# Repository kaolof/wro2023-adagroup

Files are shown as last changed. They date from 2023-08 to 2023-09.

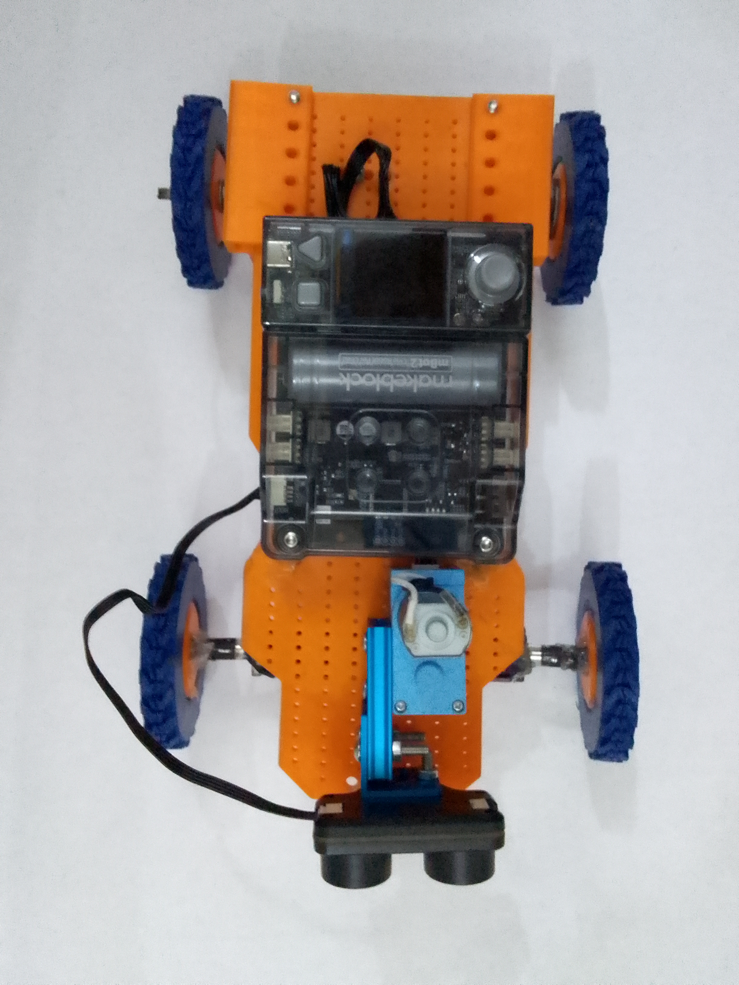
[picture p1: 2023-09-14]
v-photos/IMG_20230913_215858_856.jpg

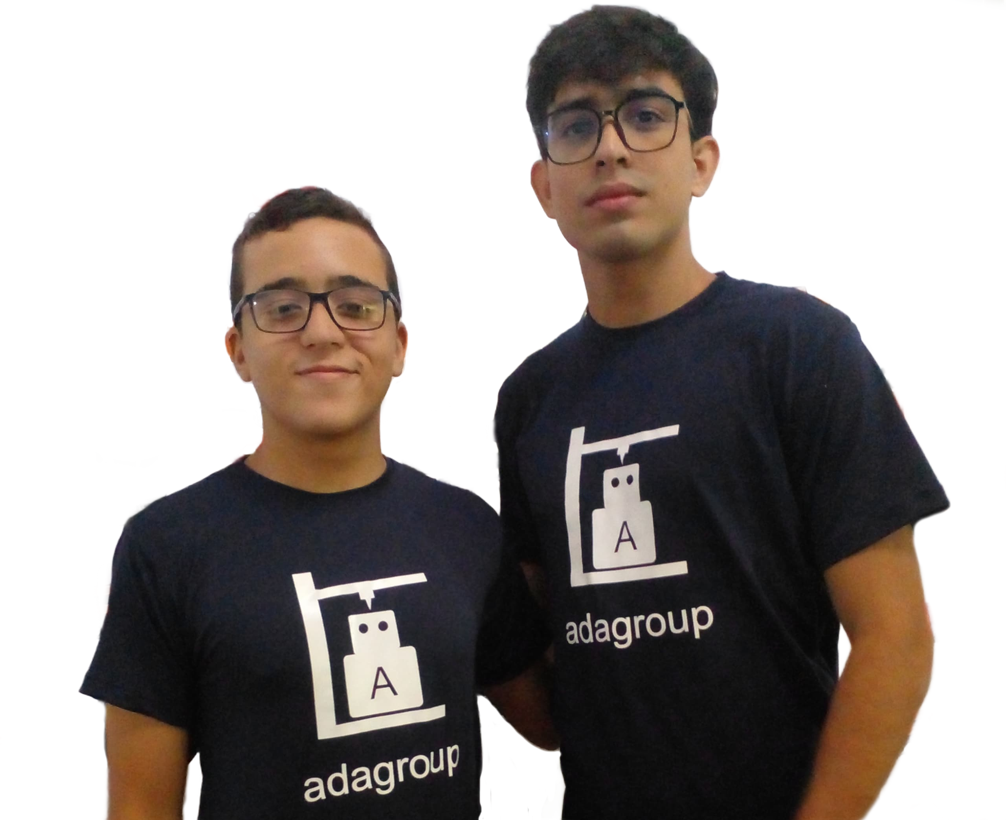
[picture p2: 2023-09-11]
t-photos/equipo.png

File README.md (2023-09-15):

# wro2023-adagroup

 <p style = "text-aling:center;">En gran mayoría de los casos siempre se llega a buscar formas de mejorar la manera de viajar de un sitio a otro, de buscar la automatización del transporte, sin embargo, los procesos que se pueden llegar a plantearse suelen ser tan contaminantes y bastante elevados al nivel económico, siempre con las presencias de modelos que no estén modulados o capacitados para entornos naturales, hace que no pueda identificar las cosas a su paso, generando más problemas a su aplicación en el campo. Los integrantes del equipo presentado llamado "adagroup", sugieren un modelo que pueda detectar obstáculos, utilizando una materia prima más ecológica, y con una estructura electromecánica, utilizando elementos electrónicos para su funcionamiento, conexión, y aumentar la efectividad de los procedimientos con programación. </p> 



## Proceso de diseño

### 1. Mecanica

#### 1.1 Dirreción del vehículo

   La dirección de la solución robótica a cual se le dio el nombre de Cybercooper es de tipo electrónica Ackermann. La dirección electrónica aporta la asistencia necesaria para mover las ruedas y efectuar el giro, esta es una gran alternativa a las direcciones mecánicas e hidráulicas porque no le causa mayor trabajo al motor y permite que tenga menos conexiones mecanicas haciendo que sea mucho más sencilla.

   Por dirección Ackermann se entiende a un sistema de direccionamiento automotriz que permite a las ruedas girar ángulos distintos con el fin de generar un solo centro de giro, otorgándole al carro un mejor desempeño en las curvas lo que hace que no se pierda velocidad mientras se gira.

   En el caso de la dirección del Cybercooper, se utilizaron estos dos sistemas para generar el direccionamiento del carro, componiéndose por 4 piezas (una mejoría ante sistema anterior), el servomotor que es el hace girar el sistema (este se encuentra ubicado en la parte superior del chasis) el cual esta conectado a una barra de madera (es quien soporta a las ruedas, esta mide 10cm de largo).

   



#### 1.2 Conducción

   El Cybercooper es propulsado por el eje trasero se compone por una transmisión de dos velocidades, donde el piñón de ataque fijado al servomotor con un tornillo acciona el engranaje coronario fijado con dos contra tuercas (dos adelante del engranaje y dos atrás) en una barra roscada (mismo diámetro que las anteriores) de 16cm de largo. 
   Al motor inducir velocidad y potencia en el engranaje coronario accionando la barra roscada y comenzando a mover las ruedas (las cuales están fijadas a cada lado de la barra), el eje de salida de la transmisión es sostenido por dos bases (impresas en 3D) donde la base más grande actúa de suspensión fija con el objetivo de reducir vibraciones en el robot. Esta se encuentra fijada con dos tornillos.

  La base más pequeña tiene una forma de "U" la cual se encarga de sujetar y mantener al engranaje coronario en la posición ideal, sin embargo al motor mover el sistema completo, aplicaba una cantidad de estrés considerable a la pieza por lo que se le colocó un resorte para darle una mayor rigidez a esta base. Además de eso, el motor esta elevado 0.5cm con una base de plástico para posicionar mejor el piñón con tal de formar un ángulo de 90° entre los dos engranajes.

  




#### 1.3 Diseño de chasis

  Ya con el sistema de conducción y dirección definidos y explicados pieza por pieza, se puede describir el diseño del chasis.
  Esta configuración que posee el Cybercooper es basada en el Cybertruck de Tesla y varios autos deportivos como por ejemplo el Bugatti, la cual consiste en una base con forma irregular hecha de PLA con un tamaño de 25cm x 10cm x 0.5cm. 

  

  En la parte trasera se encuentra un rectángulo 7.5cm x 10cm donde se encuentra la tracción de la solución robótica la cual dispone de dos pilares de 1cm x 1cm x 6cm que le dan rigidez al motor para sostenerse, y a su vez, cuenta con una serie de perforaciones de 0.2cm, más 8 huecos de 0.4cm de diámetro (2 para la suspensión fija y 4 para la base del engranaje) lo que le proporciona menos peso al vehículo. 

  

  La forma geométrica del tren trasero le proporciona mayor rigidez por lo que le permite mejorar estabilidad y evitar las vibraciones debido que se distribuye mejor el peso. 
En la parte intermedia de la pieza se encuentran 5 varillas, una en la mitad, dos formando un triángulo, y dos a los costados. El motivo de estas varillas es reducir el peso sin perder rigidez en la pieza, además de que la forma del triángulo se caracteriza por ser una de las más rígidas del mundo y es por esta razón que se posicionaron las varillas de dichas posiciones. En caso hipotético que las varillas laterales se quiebren, queda el triángulo y en caso de que éste también se desprenda, quedará la varilla central. El tamaño de ésta sección del chasis es de 7cm de largo. 

  Con esto en mente podemos pasar al tren delantero, donde reposa la transmisión que se encarga de la dirección, esta última sección cuenta con dos pilares de igual dimensión al igual que la parte trasera cumpliendo la misma función de otorgar soporte al motor, esto en el modelo antecesor, ya que el servomotor de la dirección se encuentra sobre el chasis en el nuevo modelo. Esta sección tiene una forma más estrecha en el frente, con el fin de dar mayor libertad a las ruedas y a los sensores para girar, además de reducir el peso del vehículo. En el lado derecho de esta parte reposa la dirección (esto en el modelo antecesor).  




### 2. Electrónica

#### 2.1 Sensores

   El modelo desarrollado se encuentra compuesto por sensores RGB tipo quad bayer, y un sensor ultrasónico tipo 2, desarrollados por makeblock del kit “mBot Neo 2”.

Estos sensores brindan al Cybercooper la capacidad de detectar los obstáculos que se vaya encontrando en el camino, y si este llega a ser modificado anteriormente, para que analice por donde tiene que ir, los sensores tienen la habilidad de ubicar las marcas o señales que se le indiquen al modelo para tomar acción.

 El sensor RGB se define por la identificación de colores dentro del rango RGB, en este caso, el sensor utilizado, aparte de tener dicha habilidad, posee la capacidad de brindar la luz necesaria para iluminar el modelo en general, además de que esta luz ayuda en cierto porcentaje con la detección de colores en el caso de que haya interferencia de la luz ambiental, sea existente o no.

  El sensor ultrasónico se especializa en la detección de obstáculos utilizando un sonido con rangos ultrasónicos, los cuales no son perceptibles para el ser humano, este puede calcular la distancia casi exacta entre un objeto y el dispositivo o modelo portador del sensor ultrasónico. En el caso del sensor ultrasónico tipo 2 desarrollado por makeblock, es utilizado para la detección de obstáculos a poca distancia, de 3 a 300cm, posibilitando la detección de los objetos más cercanos, a un lapso de 10 microsegundos de reacción.

  


   Aplicando estos sensores al modelo, hace que tenga la posibilidad de dar los datos necesarios e identificar los obstáculos o indicaciones presentes en múltiples casos de transporte o movimientos presentes.

   La ubicación de los sensores están situados a conexión con el tren delantero, más exacto, ubicados en el eje de dirección, debido a dos factores:

 La distancia de 5-15mm que necesita el sensor RGB para una detección precisa.
 En ángulo de inclinación hacia arriba que posee el sensor ultrasónico en su máxima detección, para una mejor detección de objetos, su ubicación que se localiza en la parte inferior, hace tener una mejor reacción.

   Por otro lado, también se encuentran los sensores aplicados al CyberPi, que ayudan con la detección de carga, y el sensor de luz integrado, además de otros sensores que detectan la carga del código presente.

   

#### 2.2 Control de Velocidad - Dirección

  Con los sensores cubiertos, es importante después de que estos provean la información necesaria, la misma sea ejecutada, y aquí es donde influyen los motores tipo codificador fotoeléctrico, los cuales poseen la filosofía de un servomotor, pero al ser utilizado a 360 grados, y se lleva a su mayor potencia (combinado con todo el peso que tiene que mover por el apartado de dirección y propulsión), lo cual hace que tenga segundos de apagado donde genere cierto tiempo para detenerse el sistema de propulsión y dirección por completo.

  Un motor de tipo codificador fotoeléctrico posee la capacidad de tener una buena precisión debido a su sistema de codificación óptica, por ello su nombre de fotoeléctrico, y no hace cumplir del todo con las características de un servomotor. Utilizando dos motores ubicados por debajo del chasis, uno conectado con el sistema de propulsión y otro conectado hacia el sistema de dirección, ubicado en la parte superior del chasis. Esto aparte de ir conectados con dichos sistemas, van conectados con el CyberPi, con el objetivo de recibir las ordenes que le dé en base al código implantado en el mismo.

  

  La ubicación que posee el motor trasero es debido a la conexión que tiene que tener con los engranajes mecánicos de la transmisión trasera, priorizando la propulsión en ambas ruedas del carro, haciendo que no se transmita de manera directa tomando en cuenta los engranajes que ayudan en la transmisión de la fuerza hacia las ruedas, incluyendo esto, el motor posee una capacidad de voltaje que va hasta los 7,4 voltios y en cuanto a su potencia es mayor a las 300 revoluciones por minuto, esto aplicado para el motor de propulsión, mientras que en la dirección se presenta de manera individual, sin el uso de engranajes que facilita tanto en fuerza como en funcionamiento, para cada caso se debe de aplicar una fuerza diferente cada vez que se haga un cambio de dirección, debido al peso de los sensores y su posición en el sistema de dirección, siendo los siguientes:
  
  

  

6 RPM para ejecución hacia la derecha

6 RPM para la ejecución hacia la izquierda

5 RPM para enderezar viniendo de la derecha

5 RPM para enderezar viniendo de la izquierda

  Por otro lado, también este es controlado por el mismo CyberPi, para hacer los cambios de dirección, parándose el sistema de propulsión, activándose el sistema de dirección, y después de girar de nuevo volver a ejecutarse.

   Además de que en tal dicho caso de que se utilice por completo el sensor ultrasónico esta dirección es accionada en base a la distancia que detecta el sensor establecido, en el rango de 75cm de distancia hacia el muro, esto puede variar de manera leve, debido a la velocidad de respuesta del sensor.    

   Aplicando esto en el ámbito físico, se expresaría un movimiento rectilíneo uniformemente variado cuando este anuló el giro anterior siendo el punto de partida hasta el punto dónde comienza a girar de nuevo, variando los valores depende de que en que momento detecte la distancia necesaria para el cambio de dirección (cuando el sensor ultrasónico detecte algo a menos de 75cm), variando la distancia.

   Además de que en en el primer movimiento este presenta al final una desaceleración mientras que en el resto de los movimientos este presenta una aceleración al inicio y una desaceleración al final. 

   Cuando este movimiento es finalizado, este continúa con otro movimiento siendo el movimiento circular uniforme, teniendo una velocidad constante, por lo tanto la aceleración tangencial sería 0, y todo esto expresado en base a conocimientos sobre cinemática, despreciando factores de relieve y fuerzas de fricción que puedan estar presentes, a continuación los cálculos pertinentes del movimiento.

   Hay que tener en cuenta que las medidas son aproximadas, debido a la irregularidades en la pista que se puedan presentar.

#### 2.3 Diagrama de Cableado

  Los cables se ajustan a las necesidades de conexión requeridos por el modelo Cybercooper, compuestos por dos cable para los servomotores “EM” y tres cables “mBuild”, que forman parte del kit “mBot Neo 2", y son compatibles con gran parte de los componentes de makeblock. Planteado de mejor manera en el siguiente diagrama:

  

  **Nota:** Es importante aclarar que para efectos de la nacional se elimino el sensor RGB y la cámara

  Para continuar leyendo dirijase a /other/diario de ingenieria.pdf

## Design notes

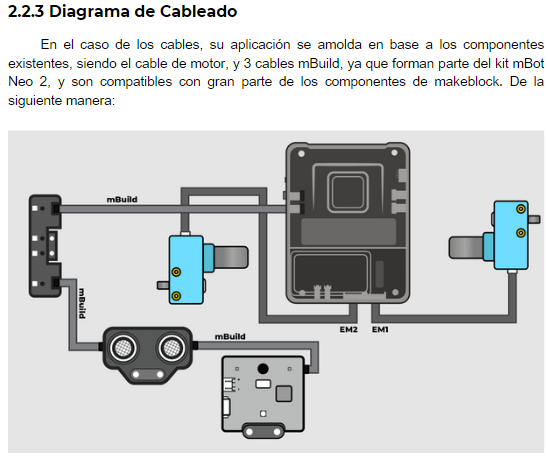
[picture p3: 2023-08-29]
schemes/esquema.png

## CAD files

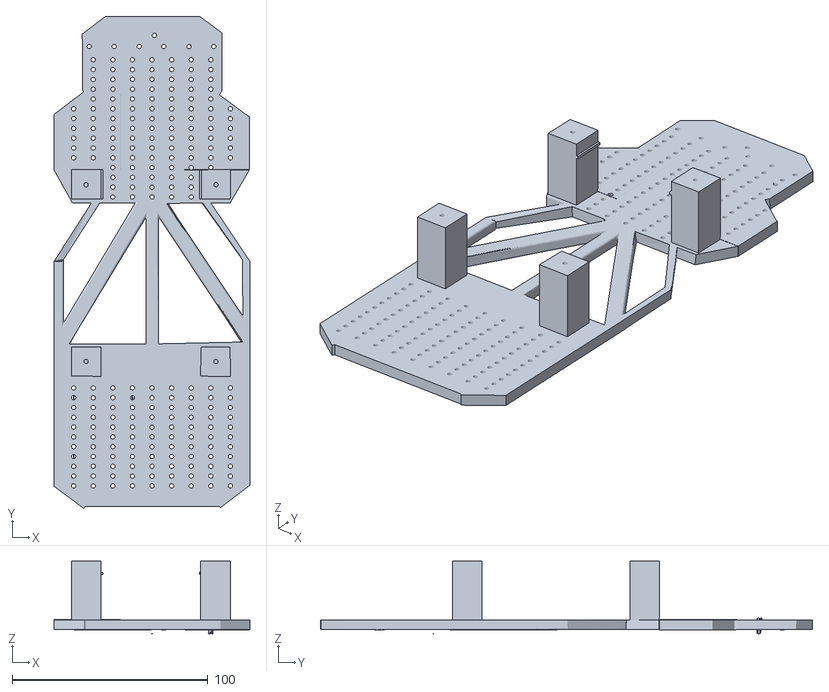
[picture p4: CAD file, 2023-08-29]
models/Modelo 3d de Cooper/Chasis.stl
100.0 x 251.1 x 37.1

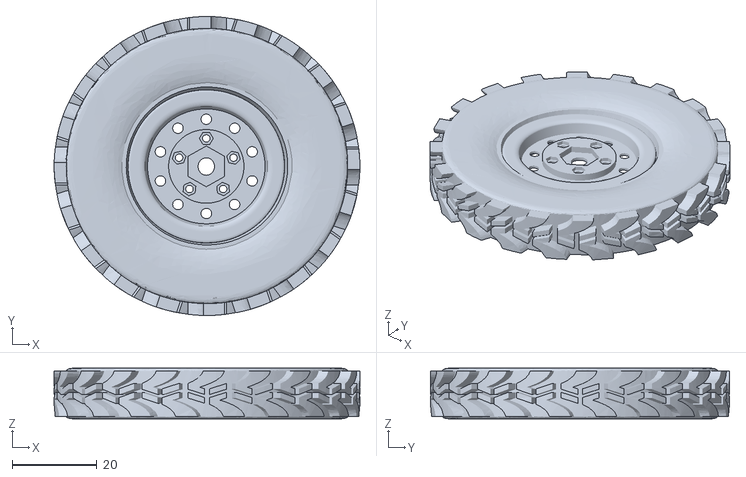
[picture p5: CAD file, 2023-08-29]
models/Modelo 3d de Cooper/Ruedas/rueda_trasera.stl
72.0 x 70.4 x 11.9

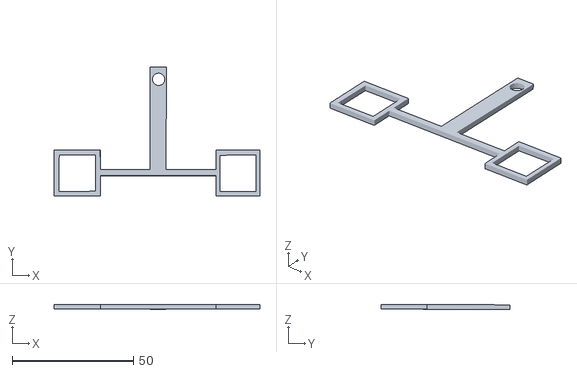
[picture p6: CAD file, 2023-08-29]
models/Modelo 3d de Cooper/Tren delantero/Bases/base dirrecional2.stl
85.0 x 53.0 x 2.21

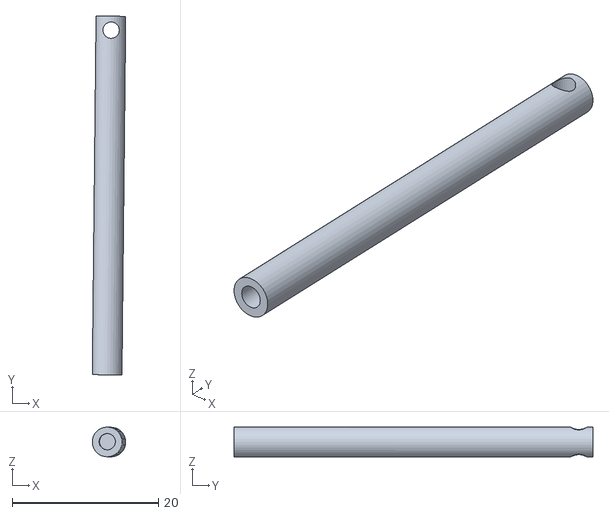
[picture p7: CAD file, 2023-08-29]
models/Modelo 3d de Cooper/Tren delantero/Ejes/union_de_las_ruedas.stl
4.57 x 49.0 x 4.08

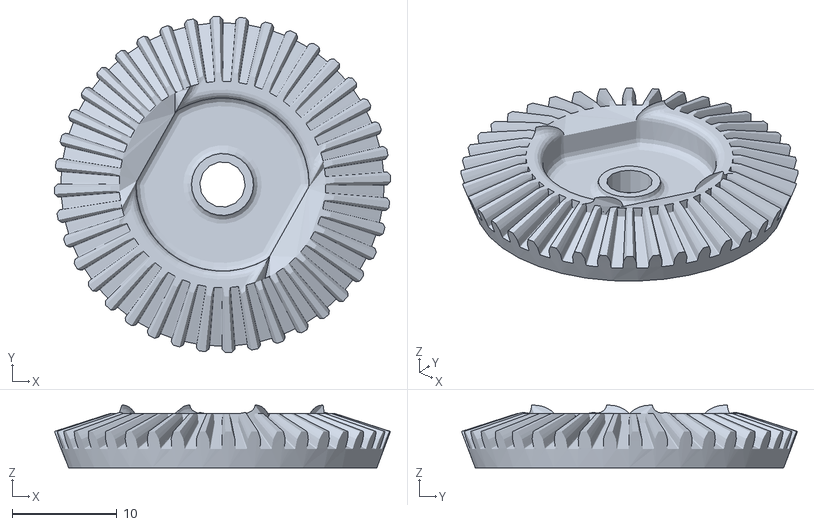
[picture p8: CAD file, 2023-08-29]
models/Modelo 3d de Cooper/Tren delantero/Engranajes/engranaje_rotatorio.stl
32.1 x 32.1 x 6.00

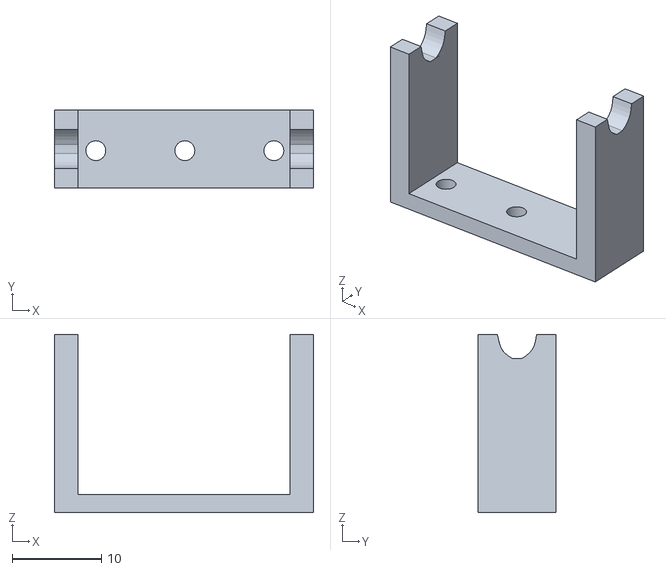
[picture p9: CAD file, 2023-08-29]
models/Modelo 3d de Cooper/Tren trasero/Bases/Base_diferencial.stl
29.1 x 8.79 x 20.0

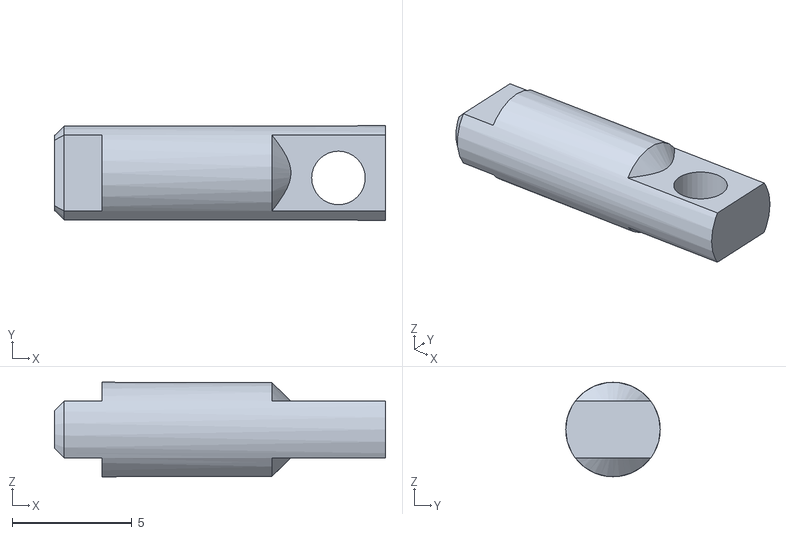
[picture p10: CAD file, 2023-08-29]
models/Modelo 3d de Cooper/Tren trasero/Ejes/union_larga.stl
13.8 x 3.95 x 3.95

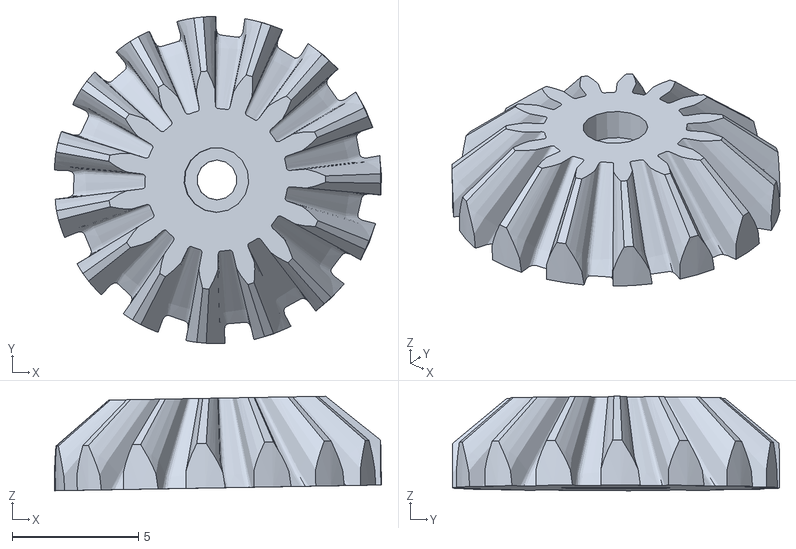
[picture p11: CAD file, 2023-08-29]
models/Modelo 3d de Cooper/Tren trasero/Engranajes/lateral.stl
12.9 x 13.0 x 3.74

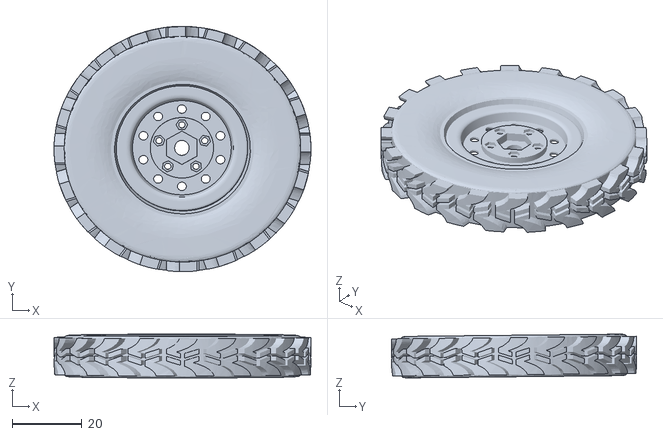
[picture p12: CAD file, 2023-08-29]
models/Modelo 3d de Cooper/Ruedas/rueda_delantera.stl
73.8 x 70.4 x 12.6

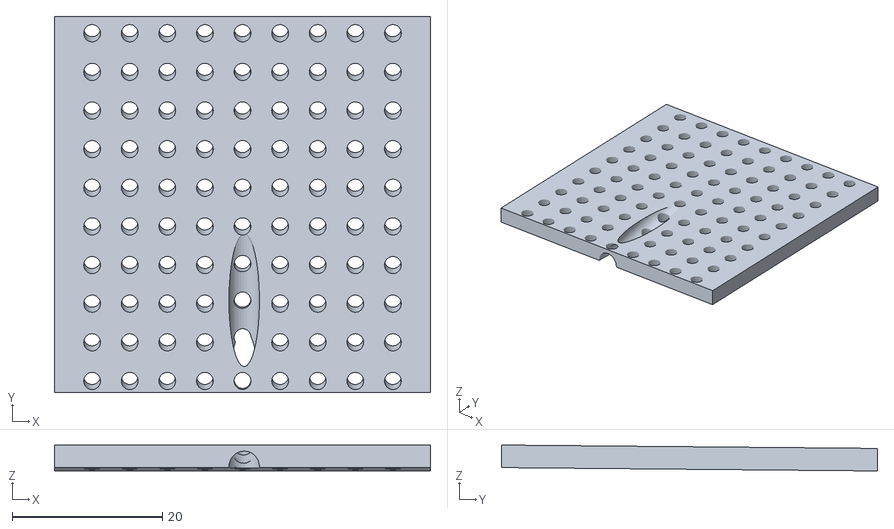
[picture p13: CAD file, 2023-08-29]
models/Modelo 3d de Cooper/Tren delantero/Bases/camara.stl
50.0 x 50.0 x 3.45

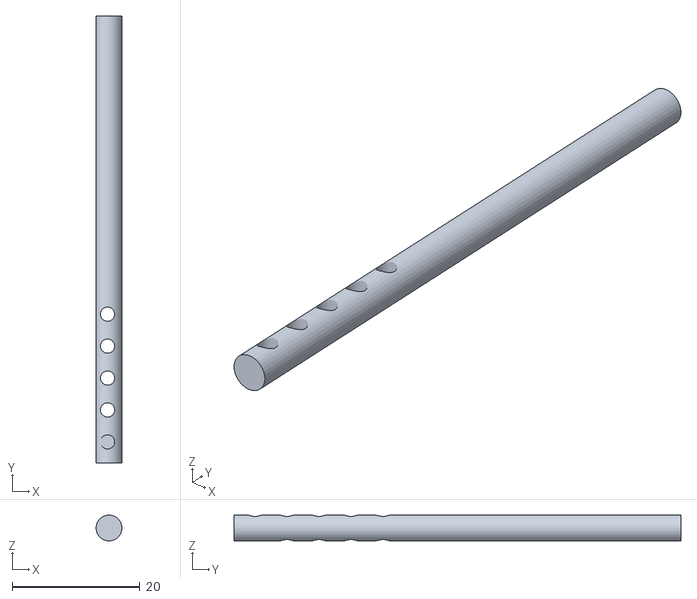
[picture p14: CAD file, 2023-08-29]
models/Modelo 3d de Cooper/Tren delantero/Ejes/eje dirrecional.stl
4.06 x 70.0 x 4.06

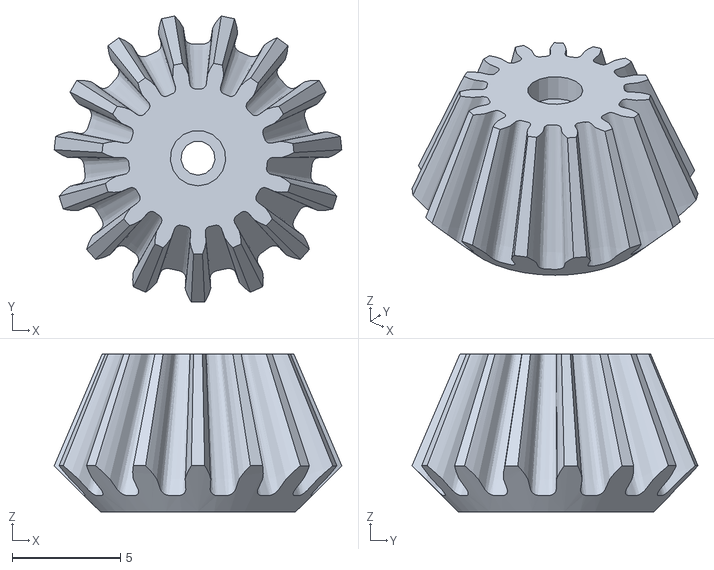
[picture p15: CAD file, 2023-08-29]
models/Modelo 3d de Cooper/Tren delantero/Engranajes/piñon.stl
13.3 x 13.2 x 7.30

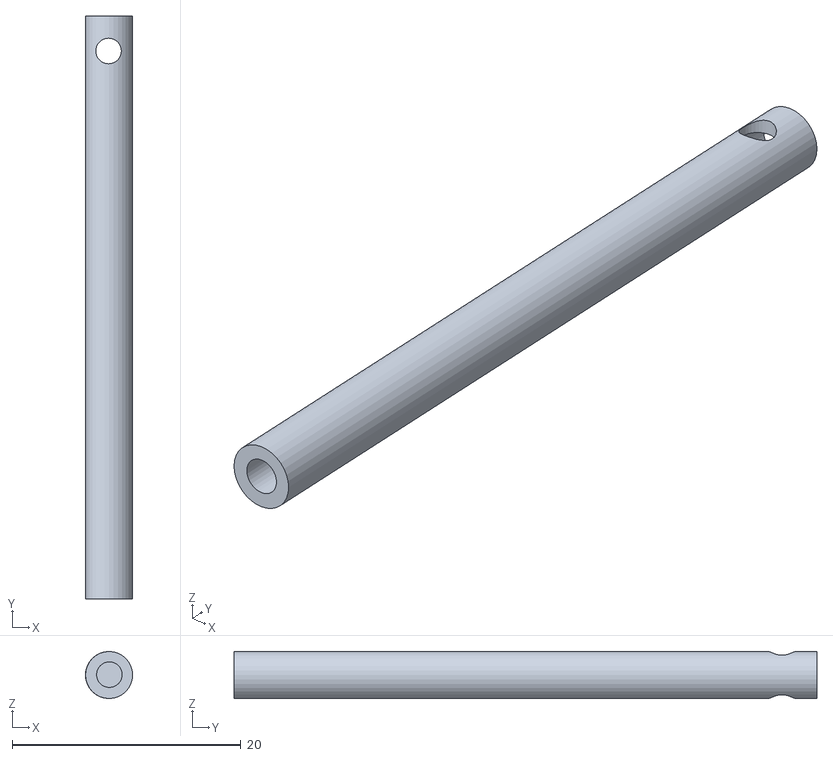
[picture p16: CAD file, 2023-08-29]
models/Modelo 3d de Cooper/Tren trasero/Ejes/EjeTI.stl
4.13 x 50.9 x 4.11

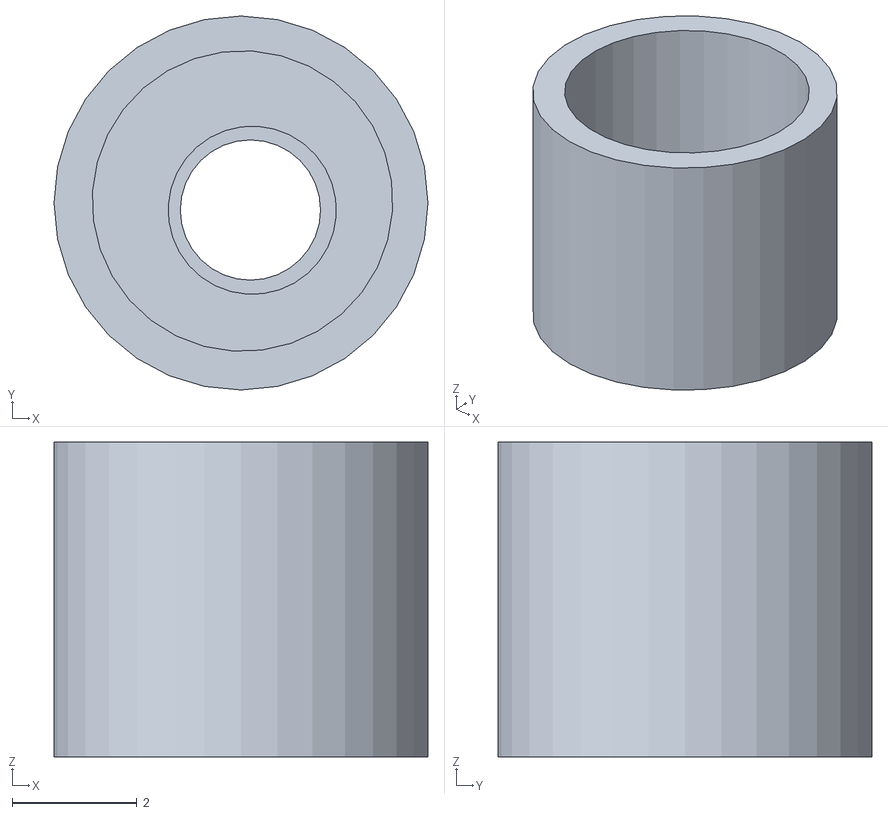
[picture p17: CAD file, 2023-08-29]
models/Modelo 3d de Cooper/Tren delantero/Bases/base dirrecional.stl
6.00 x 6.00 x 5.05

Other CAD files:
models/Modelo 3d de Cooper/Tren trasero/Engranajes/piñon.stl
models/Modelo 3d de Cooper/Tren trasero/Ejes/union_araña.stl
models/Modelo 3d de Cooper/Tren trasero/Engranajes/araña.stl
models/Modelo 3d de Cooper/Tren delantero/Bases/ultrasonico.stl
models/Modelo 3d de Cooper/Tren trasero/Ejes/EjeTD.stl
models/Modelo 3d de Cooper/Tren trasero/Engranajes/principal.stl

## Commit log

2023-08-29 updating files
    [Base_diferencial.stl, Chasis.stl, EjeTD.stl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]
2023-09-15 The code that use the ultrasonic sensor was added
